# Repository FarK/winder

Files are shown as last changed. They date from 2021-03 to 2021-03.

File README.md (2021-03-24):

Wool Winder
===========

This project consists in a series of 3D printed pieces to assembly a wool
winder. It is based on a couple of existing projects and commercial products
[1][2][3].

All the pieces are designed in order to ease the printing process. For example,
supports are not needed for any of the pieces.

The whole structure was designed in [OpenScad](https://www.openscad.org/) and
there is a lot of customizable parameters, like the gears size and angle, the
bearing and threading rod radius, the screw holes radius, etc. All these
parameters can be found at the header of the `winder.scad`.

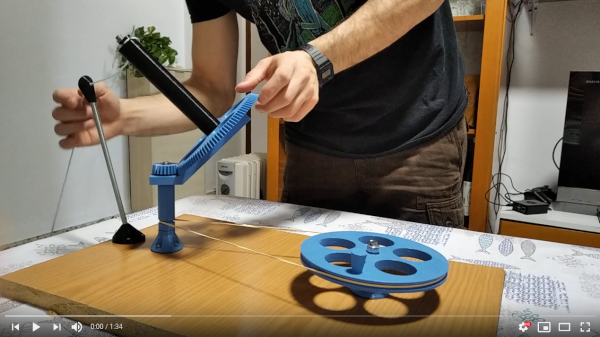
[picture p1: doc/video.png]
winder_img (https://www.youtube.com/watch?v=sXUekIx7C48)


Generation
==========
The easiest way to generate all the pieces is by using the provided makefile.
After launching the `make` command, you should find all the`*.stl` files inside
the folder `stl/`. There is an "special" `all.stl` which contains all the pieces
spread in a plane. There is another make target, `make images`, to generate a
folder with two images for each piece, one normal preview render and another
cross-section render.

You can also open `winder.scad` with OpenScad, go to the end of the file,
select the assembly module you want to generate (the ones in capitals:
`BIG_GEAR()`, `CRANK()`, `POLE()`, etc), or generate the `WINDER_SPREAD()`
module, which contains all the pieces. When using this method, **do not forget**
to hit the render button before exporting the `*.stl` in order to get a full
resolution model.

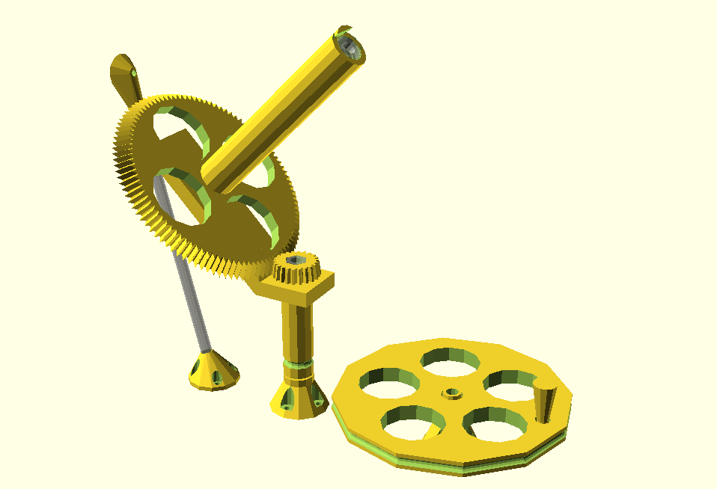
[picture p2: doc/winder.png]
winder_img
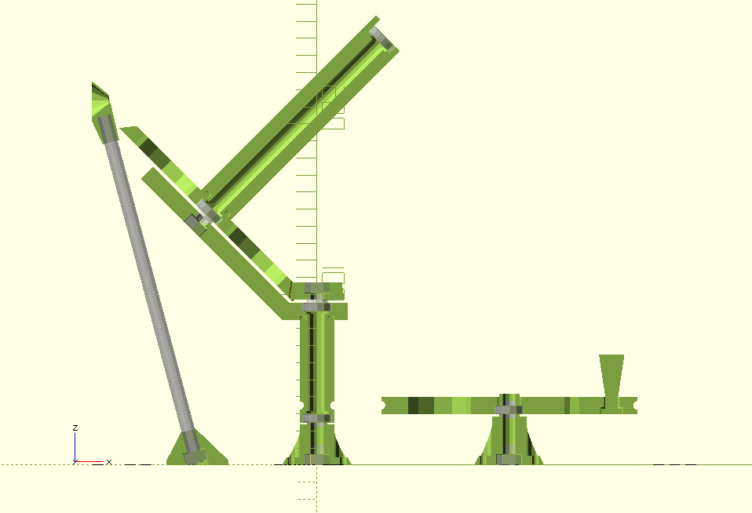
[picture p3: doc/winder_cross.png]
winder_img_cross
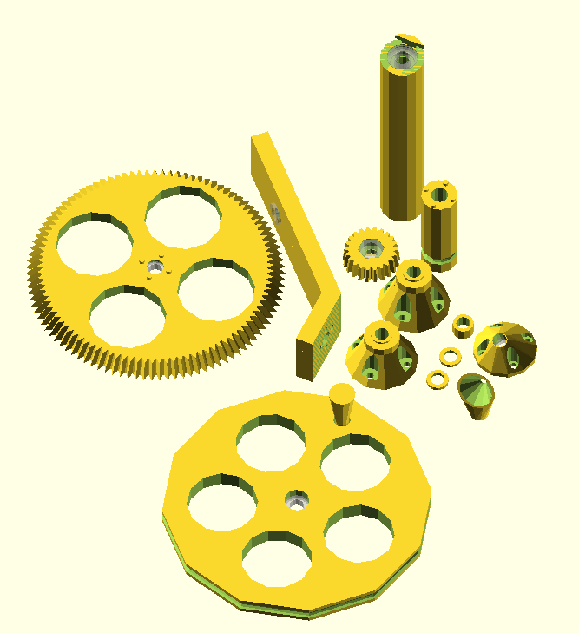
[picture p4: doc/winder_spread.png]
winder_spread
  

Guide threaded rod length
-------------------------
The length of the threaded rod for the thread guide is calculated, based on the
configured parameters, in order to put the guide at the same height of the
spinning center of the spindle.

You can find this length using the following command: `make guide_length`, or
printed in the command window of OpenScad.

Additional BoM
==============
The only not printed pieces you need for the assembly are:

* **threaded rod**: 1 m should be more than enough
* **nuts**:         7
* **bearings**:     5

You can choose the dimensions you want (i.e. bearing diameter and rod metric)
and adjust them in the configuration parameters at the top of `winder.scad`.

Assembly
========
The assembly is quite straightforward. If you take a look on the cross-section
model into OpenScad (the WINDER_SPREAD() module) and see the sample video, you
should have no problem building it by yourself.

If you perceive that the nuts unscrews with the vibrations, you may use
**self-locking nuts** or apply a bit of **nail polish** to the screw to fix it.

TODO
====

* Add a counterweight
* Support timing belt based transmission
* Support double bearing shaft for the crank

License
=======
This project is licensed under the
[GNU GPL 3.0 license](https://www.gnu.org/licenses/gpl-3.0.txt)

This project also use a **slightly modified** library made by **GregFrost** and
named **Parametric Involute Bevel and Spur Gears** for generating the bevel
gears. This library is licensed under
[GNU LGPL 2.1](https://www.gnu.org/licenses/old-licenses/lgpl-2.1.txt),
you can find a copy of this license in `LICENSE.gears.txt`. You could find the
original file here: http://www.thingiverse.com/thing:3575

References
==========
* [1]: Homemade wool winder:   https://www.youtube.com/watch?v=nJKxa9mhLuI&t=685s
* [2]: 3D printed wool winder: https://www.thingiverse.com/thing:13816
* [3]: Commercial wool winder:  https://www.youtube.com/watch?v=wf7lT6OYEQ0&t=69s

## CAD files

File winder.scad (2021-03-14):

/*
 * Wool Winder: An OpenScad script for generate a wool winder machine.
 * Copyright (C) 2021  Carlos Falgueras García
 *
 * This program is free software: you can redistribute it and/or modify it under
 * the terms of the GNU General Public License as published by the Free Software
 * Foundation, either version 3 of the License, or (at your option) any later
 * version.
 *
 * This program is distributed in the hope that it will be useful, but WITHOUT
 * ANY WARRANTY; without even the implied warranty of MERCHANTABILITY or FITNESS
 * FOR A PARTICULAR PURPOSE. See the GNU General Public License for more
 * details.
 *
 * You should have received a copy of the GNU General Public License along with
 * this program. If not, see <https://www.gnu.org/licenses/>.
 */

include<involute_gears.scad>

// This variable will be overwritten by make to choose a module

/*****************/
/* CONFIGURATION */
/*****************/
gears_big_radius   = 70;        // Radius of the big rotating gear
gears_small_radius = 15;        // Radius of the small fixed gear
gears_thickness    = 10;        // Thickness of both gears
gears_angle        = 45;        // Angle between gears
gears_pitch        = 250;       // Pitch of both gears (less teeth the bigger)

support_thickness  = 10;        // Thickness of gears support
support_clearance  = 2;         // Distance between support and gears

pole_radius        = 12.5;      // Radius of the winding pole
pole_height        = 140;       // Height of the winding pole

bearing_ext_radius = 17/2;      // External radius of bearings
bearing_int_radius = 4;         // Internal radius of bearings
bearing_thickness  = 5;         // Thickness of bearings

shaft_height       = 60;        // Height of the shaft

belt_height        = 35;        // Vertical position of the transmission belt
belt_radius        = 2.5;       // Radius for the belt guides

nut_radius         = 7.25;      // Circumcircle radius of the nuts
nut_thickness      = 6;         // Thickness of the nuts

base_screw_radius  = 2;         // Radius of screws of both bases

crank_radius       = 75;        // Radius of crank disk
crank_thickness    = 10;        // Thickness of crank disk
crank_hdl_height   = 25;        // Height of crank handle
crank_hdl_radius   = 7.5;       // Radius of crank handle

guide_angle        = 20;        // Angle of the wool guide
guide_hole_radius  = 2;         // Size of the guide hole

threaded_rod_clearance = 1.2;   // Factor for the radius of the holes for the threaded rod

ec = threaded_rod_clearance; // [GLOBAL] Edge clearance
$fa = $preview? 30: 5;
$fs = 0.1;


/*************/
/* FUNCTIONS */
/*************/
function fix_rad(r, pitch) = ceil(r * 360 / pitch) * pitch / 360;

function pitch_apex(r1, r2, ang, pitch) =
	fix_rad(r2, pitch) * sin(ang) + (fix_rad(r2, pitch) * cos(ang) +
	fix_rad(r1, pitch)) / tan(ang);

function cone_distance(r1, r2, ang, pitch) =
	sqrt(pow(pitch_apex(r1, r2, ang, pitch), 2) + pow(fix_rad(r1, pitch), 2));

function pitch_angle(r1, r2, ang, pitch) =
	asin(fix_rad(r1, pitch) / cone_distance(r1, r2, ang, pitch));

function num_teeth(r, pitch) = fix_rad(r, pitch) * 360 / pitch;

function shaft_belt_offset(t) = t*2;
function crank_belt_offset(t) = t/2;
function guide_rod_depth(r)   = r*4;
function guide_hole_offset(r) = r*2;
function guide_hole_width(r)  = r*2.5;
function guide_hole_offset_fixed(r, a) =
	guide_hole_offset(r) + guide_hole_width(r)/2*tan(a);


/*******************/
/* GENERIC MODULES */
/*******************/
module empty(); // Use this as placeholder for temporally remove a children

module torus(r1, r2) {
	rotate_extrude(convexity = 10)
		translate([r1, 0, 0])
			circle(r = r2);
}

module wheel_holes(r1, r2, n, offset=0, cl=0.8) {
	h = r2 + (r1-r2)/2;
	step = 360/n;
	r = min(h * sin(step/2*cl), (r1-r2)/2*cl);
	difference() {
		children(0);
		for (i = [0:n-1])
			rotate([0, 0, offset+i*step])
				translate([h, 0, 0])
					cylinder(r=r, h=1000, center=true);
	}
}

module big_gear_origin(r1, r2, ang, pitch) {
	pitch_apex1  = pitch_apex(r1, r2, ang, pitch);
	pitch_apex2  = pitch_apex(r2, r1, ang, pitch);
	pitch_angle1 = pitch_angle(r1, r2, ang, pitch);
	pitch_angle2 = pitch_angle(r2, r1, ang, pitch);

	translate ([0,0,pitch_apex1])
	rotate([0,-(pitch_angle1+pitch_angle2),0])
	translate([0,0,-pitch_apex2])
		children();
}

module small_gear(r1, r2, r3, h, ang, pitch) {
	difference() {
		bevel_gear (
			number_of_teeth = num_teeth(r1, pitch),
			cone_distance = cone_distance(r1, r2, ang, pitch),
			outside_circular_pitch = pitch,
			face_width = h,
			$fn = $preview? 5 : 15
		);
		cylinder(r=r3, h=50);
		translate([0, 0, h]) mirror([0, 0, 1]) children(0);
	}
}

module big_gear(r1, r2, r3, h, ang, pitch) {
	wheel_holes(r2, r3, 4)
	difference() {
		bevel_gear (
			number_of_teeth = num_teeth(r2, pitch),
			cone_distance = cone_distance(r1, r2, ang, pitch),
			outside_circular_pitch = pitch,
			face_width = h,
			backlash = 1,
			$fn = $preview? 3 : 15
		) {
			children(1);
			children(2);
		}
		mirror([0, 0, 1])
			children(0);
	}
}

module pole(r1, r2, h) {
	$fn = $preview? 15 : 0;
	difference() {
		cylinder(r=r2, h=h);
		cylinder(r=r1*ec, h=h*4, center=true);
		children(0);
		translate([0, 0, h])
			children(1);
	}
	translate([0, 0, h]) {
		difference() {
			cylinder(r=r2, h=5);
			cylinder(r=r1*ec, h=20, center=true);
			translate([-r2, -r2, -2.5])
				cube([r2*1.7, r2*2, 10]);
			translate([-r2, -r2, 0])
				cube([r2*2, r2*2/3, 2]);
			translate([-r2, r2/3, 0])
				cube([r2*2, r2*2/3, 2]);
		}
	}
}

module gears_support(r1, r2, r3, h, ang, pitch, clearance) {
	hcl  = h+clearance;
	r1cl = r1*1.2;
	r2cl = r2*1.2;

	translate([0, 0, hcl]) {
	difference() {
		union() {
		difference() {
			translate([-r1cl, -r1cl, -hcl]) {
				cube([2*r1cl, 2*r1cl, h]);
			}
			translate([0, 0, -clearance])
				children(1);
		}

		difference() {
			big_gear_origin(r1, r2, ang, pitch) {
				translate([-r2cl, -r1cl, -hcl]) {
					difference() {
						cube([r2cl*1.5, r1cl*2, h]);
						translate([r2cl, r1cl, h])
							cylinder(r=r3, h=50, center=true);
						translate([r2cl, r1cl, 0])
						rotate([0, 0, 90])
							children(3);
					}
				}
				translate([0, 0, -clearance])
					children(4);
			}

			translate([-r1cl*2, -r1cl*2, -clearance-h*5])
				cube([4*r1cl, 4*r1cl, h*4]);
		}
		}
		translate([0, 0, -hcl])
			children(2);
	}
	children(0);
	translate([0, 0, -clearance])
		children(4);
	}
}

module washer(r1, r2, h) {
	difference() {
		cylinder(r=r1, h=h);
		cylinder(r=r2, h=h*4, center=true);
	}
}

module bearing(r1, r2, h) {
	difference() {
		union() {
			difference() {
				cylinder(r=r1, h=h);
				translate([0, 0, -h/2])
					cylinder(r=r1*0.9, h=h*2);
			}
			cylinder(r=r2*1.1, h=h);
			translate([0, 0, h*0.1])
				cylinder(r=r1, h=h*0.8);
		}
		translate([0, 0, -h/2])
			cylinder(r=r2, h=h*2);
	}
}

module bearing_hole(r1, r2, h, clearance, open = false) {
	ro = r2+(r1-r2)*2/3;
	ri = open? ro : r2*ec;
	mirror([0, 0, 1]) {
		cylinder(r=r1*clearance, h=h*2, center=true);
		cylinder(r=ro, h=h*1.3);
		cylinder(r=ri, h=h*20);
		%bearing(r1, r2, h);
	}
}

module base(r1, r2, r3, h) {
	h1 = h*1/4;
	h2 = h*3/4;
	r4 = r1*2;

	difference() {
		difference() {
			union() {
				translate([0, 0, h2]) {
					cylinder(r=r1, h=h1*0.80);
					cylinder(r=r2+(r1-r2)*1/3, h=h1);
				}
				cylinder(r1=r4, r2=r1, h=h2);
			}
			cylinder(r=r2, h=(h1+h2)*4, center=true);
			children(0);
		}

		for (i = [0:4]) {
			rotate([0, 0, i*90]) {
				translate([r1 + (r4 - r1)/2, 0, h2*1/4]) {
					cylinder(r=r3*2.5, h=h2);
					translate([0, 0, -h2/2])
						cylinder(r=r3, h=h2);
				}
			}
		}
	}

	translate([0, 0, h])
		children(1);
}

module shaft(r1, r2, r3, h1, h2) {
	difference() {
		cylinder(r=r1, h=h1);
		translate([0, 0, h2])
			torus(r1, r3);
		mirror([0,0,1])
			children(0);
		cylinder(r=r2*ec, h=h1*4, center=true);
	}
	translate([0, 0, h1]) {
		children(1);
		children(2);
	}
}

module pins(r1, r2, h, hole=false) {
	r2 = hole? r2*1.3 : r2;
	h  = hole? h*2.3  : h;

	for (i = [0:4])
		rotate([0, 0, i*90])
			translate([r1*0.8, 0, 0])
				cylinder(r=r2, h=h, center=hole, $fn=20);
}

module nut(r1, r2, h, hole=false) {
	if (hole) {
		translate([0, 0, h*0.1])
			cylinder(r=r1*1.04, h=h*2, $fn = 6, center=true);
	} else {
		difference() {
			cylinder(r=r1, h=h, $fn = 6);
			cylinder(r=r2, h=h*4, center=true);
		}
	}
}

module crank(r1, r2, r3, h1, h2) {
	r4 = r2*0.8;
	r5 = r2*0.5;
	wheel_holes(r1, r2, 5, offset=45)
	difference() {
		cylinder(r=r1, h=h1);
		mirror([0, 0, 1])
			children(0);
		translate([0, 0, crank_belt_offset(h1)])
			torus(r1, r3);
		translate([r1*0.8, 0, 0]) {
			crank_handle(r4, r5, r2, h1, h2, 1);
		}
	}
	children(1);
	translate([r1*0.8, 0, 0])
		crank_handle(r4, r5, r2, h1, h2);
}

module crank_handle(r1, r2, r3, h1, h2, cl=0) {
	cylinder(r=r2+cl, h=h1*1.1);
	cylinder(r=r1+cl, h=h1*0.3+cl);
	translate([0, 0, h1])
		cylinder(r1=r2, r2=r3, h=h2);
}
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

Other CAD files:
involute_gears.scad
